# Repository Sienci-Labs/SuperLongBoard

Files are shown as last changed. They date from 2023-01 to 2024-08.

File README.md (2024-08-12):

# SuperLongBoard PCB Design

These are all the raw build files that we're making available to the public so you can see and access the work that's been put in to make the SuperLongBoard as it currently exists. If you'd like to make it yourself, modify it, or suggest improvements feel free. Please note and respect the license we've chosen to distribute it under.

# License

This code has been created within the context of Open Hardware and is licensed under the "CERN-OHL-S v2". Please read more about this in the LICENSE file. You could redistribute and modify this source and make products using it under the terms of the CERN-OHL-S v2. This means stuff like licensing your changes reciprocally, giving attribution to us, and releasing hardware that this code runs on as CERN-OHL-S v2 too. Note that this LICENSE applies on all coding work done in prior commits to-date, and is now being released in good faith that no action will be taken to pursue past work in order to duplicate the work we've put in without having to abide by the License that's now being applied at its first public release.

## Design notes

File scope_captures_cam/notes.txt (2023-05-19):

While running 100mm diamond pattern (all motors move at once.)
SDS00001 - Yellow Cap near X driver, Purple Cap near Y2 Driver
SDS00002 to SDS00007 - Yellow R68, Purple R67
SDS00008 to SDS00010 - Same nets as above, other side of L13
SDS00011 - Add blue on R68, Green on R67. Nothing running.
SDS00012 to SDS00014 - Same as 11, but running steppers only.
SDS00015 to SDS00023 - Same as above, spindle running.

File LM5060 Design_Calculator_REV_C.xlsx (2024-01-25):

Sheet: Instructions
 | © 2014
LM5060 Design Tool- Rev. C
Typical design procedure
Typical applications require multiple passes through the design tool using MOSFET factors such as transient
thermal response and safe operating area curves. Refer to the following application reports for more detail.
LM5060 Datasheet (See "Detailed Design Procedure") (http://www.ti.com/lit/gpn/lm5060)
The basic design process follows:
1. Enter operating conditions.
2. Select MOSFET and current limit parameters.
3. Enter desired UVLO and OVLO values to get recommended resistor values.
4. Review Circuit Characteristics
Notes
1. This worksheet is designed for use with Microsoft Excel 5.0 or later. Its use is intended to assist power supply designers in their
routine, day-to-day calculations.
2. All worksheets have light green inputs cells, white calculated cells, yellow warning cells and red high-risk cells.
3. Formulas and device constants used in the spreadsheet are locked to prohibit them from accidentally being overwritten or deleted.
TEXAS INSTRUMENTS TEXT FILE LICENSE Copyright (c) 2014 Texas Instruments Incorporated All rights reserved not granted herein. Limited License. Texas Instruments Incorporated grants a world-wide, royalty-free, non-exclusive license under copyrights and patents it now or hereafter owns or controls to make, have made, use, import, offer to sell and sell ("Utilize") this software subject to the terms herein. With respect to the foregoing patent license, such license is granted solely to the extent that any such patent is necessary to Utilize the software alone. The patent license shall not apply to any combinations which include this software, other than combinations with devices manufactured by or for TI (“TI Devices”). No hardware patent is licensed hereunder. Redistributions must preserve existing copyright notices and reproduce this license (including the above copyright notice and the disclaimer and (if applicable) source code license limitations below) in the documentation and/or other materials provided with the distribution Redistribution and use in binary form, without modification, are permitted provided that the following conditions are met: * No reverse engineering, decompilation, or disassembly of this software is permitted with respect to any software provided in binary form. * any redistribution and use are licensed by TI for use only with TI Devices. * Nothing shall obligate TI to provide you with source code for the software licensed and provided to you in obje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

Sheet: Design Calculator
LM5060 Hot Swap Design Tool
 | www.ti.com/hotswap
 |  |  | Enter Values in Green Shaded Cells
 |  |  | Calculated Values are shown in White Cells
 |  |  | Yellow and Red cells highlight potential issues with the design. Red highlights items that are higher risk.
 | Step 0: Calculator Tutorials |  | Note: Before proceeding, please watch the video tutorials listed to ensure accurate results from this tool!
 |  |  | Steps 1 & 2: Operating Conditions, Current Limit, & Circuit Breaker (7:41) (https://training.ti.com/node/1133677)
 |  |  | Step 3: MOSFET Selection (9:58) (https://training.ti.com/node/1133673)
 |  |  | Step 4: Startup (10:32) (https://training.ti.com/node/1133664)
 |  |  | Step 5: UVLO, OVLO & PGD Thresholds (4:20) (https://training.ti.com/node/1133681)
 |  |  | LM5060 Datasheet (http://www.ti.com/product/lm5060)
 |  |  | I understand and agree to watch the video tutorials if help is needed. (Choose Yes to enable the calculator.) |  |  | Yes |  |  |  |  | No
 |  |  | Assure to follow the layout and application guidelines listed on the datasheet. |  |  | Yes
 |  |  | *For additional questions not addressed in the videos, please post on E2E.ti.com |  |  |  |  |  |  |  | Yes
 | Step 1: Operating Conditions |  |  | Minimum Input Operating Voltage: VIN(MIN) | 5.5 | V
 |  |  |  | Nominal Input Operating Voltage: VIN(NOM) | 24 | V
 |  |  |  | Maximum Input Operating Voltage: VIN(MAX) | 28 | V
 |  |  |  | Worst Case Reverse Polarity Voltage | 0 | V
 |  |  |  | Maximum Load Current: IOUT(MAX) | 8 | A
 |  |  |  | Maximum Output Load Capacitance: Cload | 2000 | µF
 | Steps 1 & 2: Operating Conditions, Current Limit, & Circuit Breaker (https://training.ti.com/node/1133677) |  |  | Maximum Ambient Operating Temperature: TMAX | 100 | oC
 | Step 2: MOSFET Selection + Current Limit |  |  | Reverse Polarity | NO |  |  |  |  |  | NO
 |  |  |  | MOSFET Name | IRFH7004TRPBF |  |  |  |  |  | YES
 |  |  |  | Back to Back FETs? | NO
 |  |  |  | # of Parallel FETs | 1
 |  |  |  | Minimum Output Pin Resistance | 0 | kΩ
 |  |  |  | Output Pin Resistance: Rout | 10 | kΩ
 |  |  |  | T = 25C Rds-on typical | 1.1 | mΩ
 | Steps 1 & 2: Operating Conditions, Current Limit, & Circuit Breaker (https://training.ti.com/node/1133677) |  |  | T = 25C Rds-on max | 1.1 | mΩ
 |  |  |  | Calculated estimate of T = 25C Rds-on min | 1.1 | mΩ
 |  |  |  | Normalized Rds-on coefficient at Tmin | 1.1
 |  |  |  | Normalized Rds-on coefficient at Tmax | 1.1
 |  |  |  | Rs min (calculated) | 1.23 | kΩ
 |  |  |  | Actual Rs used | 3 | kΩ
 |  |  |  | Minimum Worst-Case Overcurrent Threshold | 27.93 | A
 |  |  |  | Typical Overcurrent Threshold | 43.64 | A
 | Step 3: MOSFET Selection (https://training.ti.com/node/1133673) |  |  | Maximum Worst-Case Overcurrent Threshold | 50.41 | A
 | Step 3: Fault Detection Delay Time |  |  | Gate Charge at Mosfet Vgs= 6.5 Volts | 10.00 | nC |  |  |  |  | NO
 |  |  |  | Safety Margin | 1.5 |  |  |  |  |  | YES
 |  |  |  | Gate Charge at Mosfet Vgs= 6.5 Volts With Margin | 15 | nC
 |  |  |  | Inrush Current Control | YES
 |  |  |  | Desired Maximum Inrush Current | 10000 | mA
 |  |  |  | Recommended Capacitance CGate | 6.2 | nF
 |  |  |  | Actual Capacitor CGate | 4.7 | nF
 |  |  |  | Actual Maximum Inrush Current | 13191.48936 | mA
 | Step 4: Startup (https://training.ti.com/node/1133664) |  |  | Calculated Maximum Slew Rate | 6.595744681 | V/ms
 |  |  |  | Maximum Startup Time | 6.11 | ms
 |  |  |  | Typical Startup Time | 6.30 | ms
 |  |  |  | Minimum Startup Time | 2.97 | ms
 |  |  |  | Minimum Timer Capacitance Ctimer | 21.40 | nF
 |  |  |  | Actual Used Timer Capacitance | 47 | nF
 |  |  |  | Startup Fault Delay Time(Min) | 13.43 | ms
 |  |  |  | Startup Fault Delay Time(Typical) | 15.67 | ms
 |  |  |  | Startup Fault Delay Time(Max) | 23.50 | ms
 |  |  |  | Over-Current Fault Delay Time(Min) | 7.23 | ms
 |  |  |  | Over-Current Fault Delay Time(Typical) | 8.55 | ms
 |  |  |  | Over-Current Fault Delay Time(Max) | 11.06 | ms
 | Step 5: UVLO & OVLO Thresholds |  |  |  | Option A |  |  |  | OPTION A |  | Option A
 |  |  |  |  | Include Hystersis |  |  |  |  |  | Option B
 |  |  |  | Desired Typical OVLO | 28 | V |  |  |  |  | Include Hystersis
 |  |  |  | Desired Typical UVLO | 9 | V |  |  |  |  | No Hysteresis
 |  |  |  | R1 | 20 | kW
 |  |  |  | Recommended Resistance for: R2 | 2.25 | kW
 |  |  |  | Enter the Resistance for R2 | 2.7 | kW
 | Step 5: UVLO, OVLO & PGD Thresholds (https://training.ti.com/node/1133681) |  |  |  | 15.00 | kW
 |  |  |  | Recommended Resistance for R3 | 1.49 | kW
 |  |  |  | Enter the Resistance for R3 | 1.8 | kW
 |  |  |  |  |  |  |  |  | OPTION B
 |  | Resulting Thresholds: | Minimum | Typical | Maximum
 |  | Upper OVLO Threshold = | 25.66 | 27.33 | 29.00 | V
 |  | Lower OVLO Threshold = | 22.40 | 24.07 | 25.73 | V
 |  | Upper UVLO Threshold = | 7.97 | 8.82 | 9.67 | V
 |  | Lower UVLO Threshold = | 6.95 | 8.02 | 9.14 | V
 |  | Note: If any of the cells above are yellow, then these values are outside of the device's operating range. This will result in the device turning either on or off at its operating limits rather than at the user selected values in yellow.
 | Design Summary |  |  | R1 = | 20 | kW
 |  |  |  | R2 = | 2.70 | kW |  |  | Settings | Units
 |  |  |  | R3 = | 1.8 | kW |  | Typical Over-Current Threshold | 43.64 | A
 |  |  |  | Rs = | 3.00 | kW |  | Startup Delay Time | 15.67 | ms
 |  |  |  | R5= | 0 | kW |  | Over-Current Fault Delay | 8.55 | ms
 |  |  |  | R8 = | 1.8 | kW |  | Upper OVLO Threshold | 27.33 | V
 |  |  |  | R9 = | 2.7 | kW |  | Lower OVLO Threshold | 24.07 | V
 |  |  |  | R10 = | 2.7 | kW |  | Upper UVLO Threshold | 8.82 | V
 |  |  |  | R11 = | 1.8 | kW |  | Lower UVLO Threshold | 8.02 | V
 |  |  |  | CTimer = | 47.00 | nF | OPTION B
 |  |  |  | Cin = | 100 | nF
 |  |  |  | CGate = | 4.7 | nF
 |  |  |  | CLoad = | 2000 | µF
 |  |  |  | D1 | SMBJ51A-13-F
 |  |  |  | Q1 | IRFH7004TRPBF
 | Notes: | 1. Although not mandatory, Cin provides transient suppression at the VIN pin
 |  | 2. A TVS clamp from VIN to GND is absolutely mandatory to clamp the voltage overshoot upon MOSFET turn-off, e.g. during circuit breaker
 |  | 3. Componet tolerances not accounted for in Min/Max Calculations.

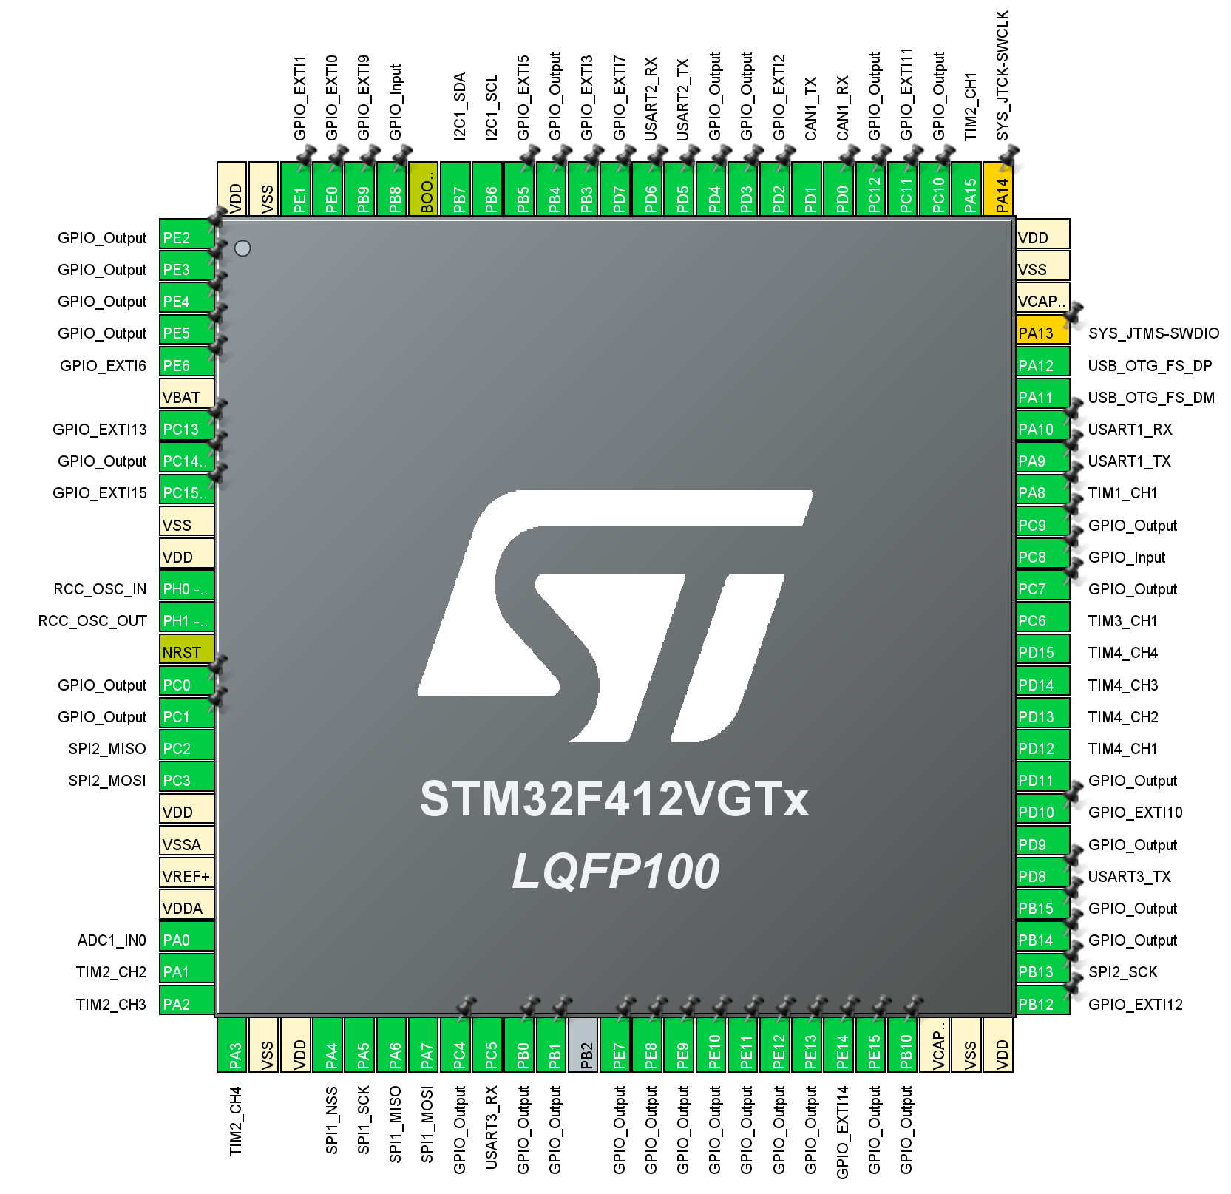
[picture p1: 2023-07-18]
Schematic/stm32f412_img.png

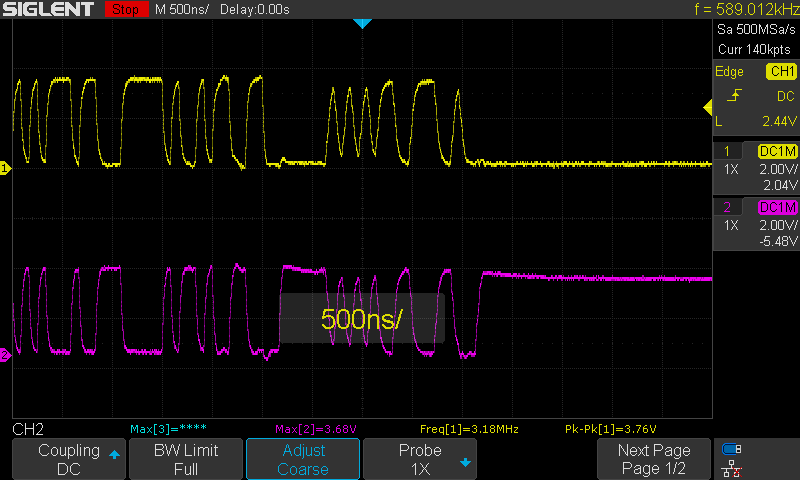
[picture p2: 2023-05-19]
scope_captures_cam/SDS00006.png

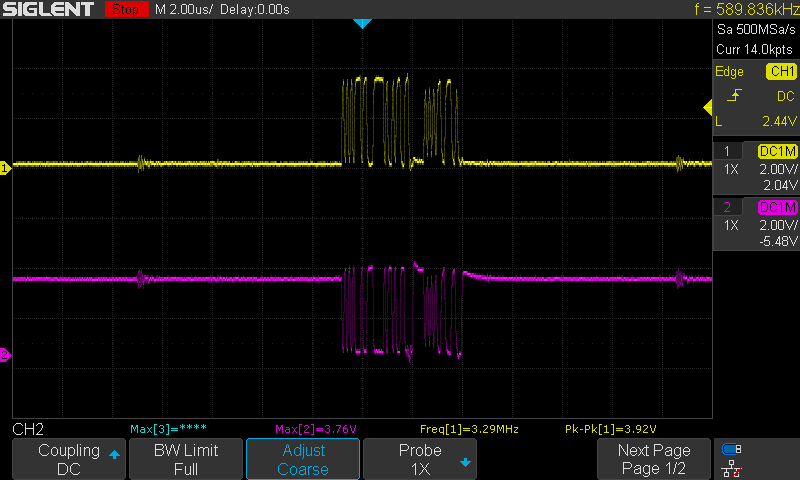
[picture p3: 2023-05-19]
scope_captures_cam/SDS00008.png

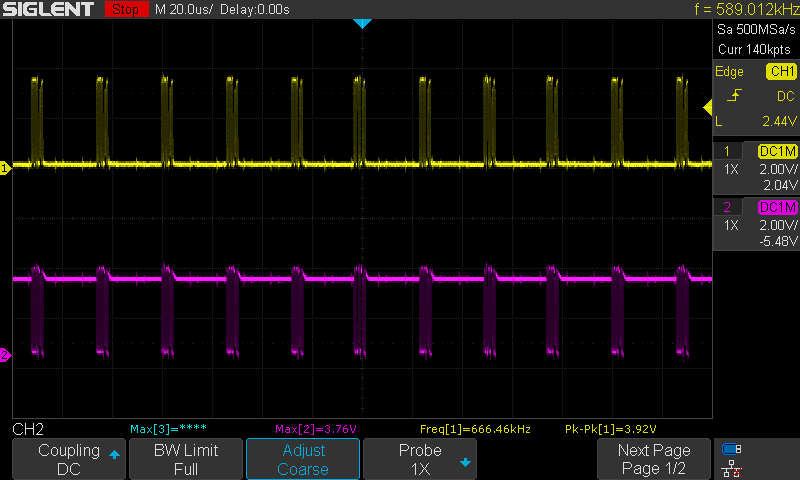
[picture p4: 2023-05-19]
scope_captures_cam/SDS00005.png

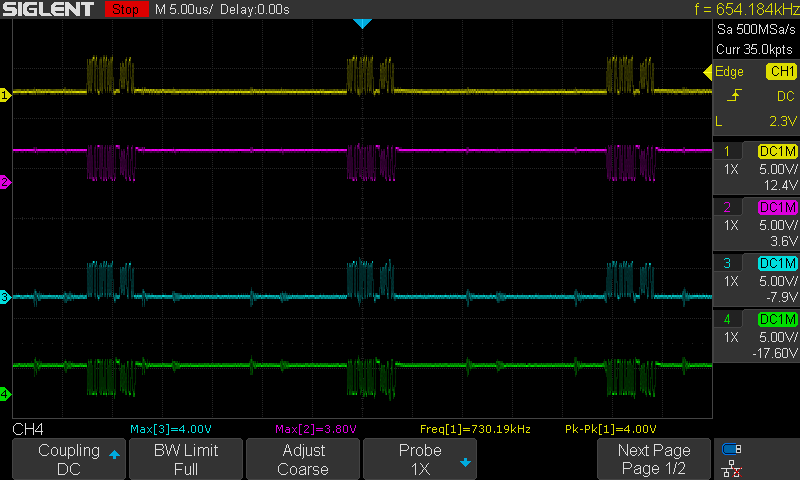
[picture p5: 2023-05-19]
scope_captures_cam/SDS00023.png

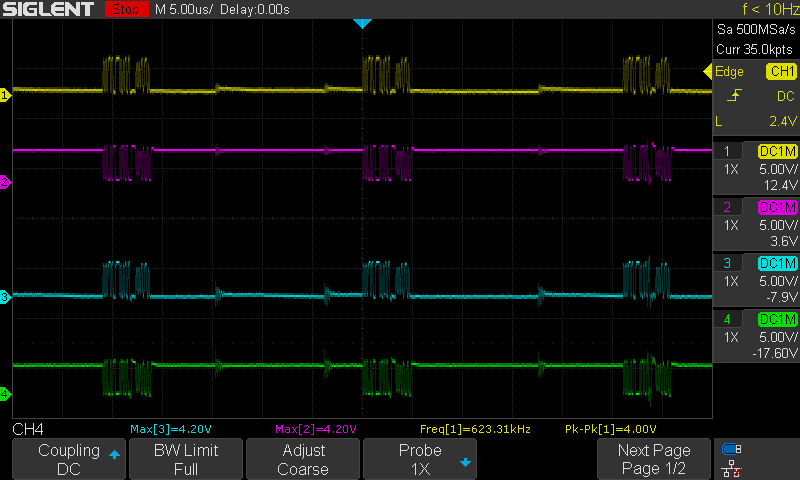
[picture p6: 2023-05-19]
scope_captures_cam/SDS00011.png

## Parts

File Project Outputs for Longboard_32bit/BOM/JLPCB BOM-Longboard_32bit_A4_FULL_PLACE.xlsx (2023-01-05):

Quantity | Manufacturer Part Number | Manufacturer | Description | SuppliersPartNumber | Designator | Comment
70 | CC0603KRX7R9BB104 | YAGEO | Chip capacitors | C14663 | C1, C2, C3_AL, C3_PH_CY, C3_PH_HLT, C3_PH_MA1, C3_PH_MA2, C3_PRB, C3_TLO, C3_XL, C3_Y1L, C3_Y2L, C3_ZL, C4, C10, C20, C21, C22, C24, C29, C30, C31, C32, C33, C34, C35, C36, C37, C42_STEP_A, C42_STEP_X, C42_STEP_Y, C42_STEP_Z, C45_STEP_A, C45_STEP_X, C45_STEP_Y, C45_STEP_Z, C46_STEP_A, C46_STEP_X, C46_STEP_Y, C46_STEP_Z, C47_STEP_A, C47_STEP_X, C47_STEP_Y, C47_STEP_Z, C50_STEP_A, C50_STEP_X, C50_STEP_Y, C50_STEP_Z, C51_STEP_A, C51_STEP_X, C51_STEP_Y, C51_STEP_Z, C65, C66, C68, C69, C70, C71, C72, C73, C80, C81, C82, C86, C90, C93, C94, C95, C96, C99 | 100nF
17 | CL10A105KB8NNNC | Samsung Electro-Mechanics | Chip capacitors | C15849 | C5, C9, C27, C28, C41_STEP_A, C41_STEP_X, C41_STEP_Y, C41_STEP_Z, C62, C63, C64, C67, C74, C85, C89, C92, C98 | 1uF
8 | CL31A106KBHNNNE | Samsung Electro-Mechanics | Chip capacitors | C13585 | C6, C11, C12, C14, C15, C58, C59, C78 | 10uF
2 | CL21A475KAQNNNE | Samsung Electro-Mechanics | Chip capacitors | C1779 | C7, C60 | 4.7uF
9 | CL21A226MAQNNNE | Samsung Electro-Mechanics | Chip capacitors | C45783 | C8, C13, C52, C53, C55, C61, C79, C83, C87 | 22uF
2 | 0603B103K500NT | Guangdong Fenghua Advanced Tech | Chip capacitors | C57112 | C16, C97 | 10nF
5 | CL10C100JB8NNNC | Samsung Electro-Mechanics | Chip capacitors | C1634 | C17, C38, C39, C75, C76 | 10pF
2 | CC0603KRX7R9BB822 | YAGEO | 50V 8.2nF X7R ±10% 0603 Multilayer Ceramic Capacitors MLCC - SMD/SMT ROHS | C113812 | C18, C19 | 8.2nF
7 | CL10A475KO8NNNC | Samsung Electro-Mechanics | Chip capacitors | C19666 | C23, C25, C26, C54, C84, C88, C91 | 4.7uF
4 | CL10B224KA8NNNC | Samsung Electro-Mechanics | Chip capacitors | C21120 | C40_STEP_A, C40_STEP_X, C40_STEP_Y, C40_STEP_Z | 220nF
8 | UUD1H221MNL1GS | Nichicon | CAP ALUM 220UF 20% 50V SMD | C125976 | C43_STEP_A, C43_STEP_X, C43_STEP_Y, C43_STEP_Z, C44_STEP_A, C44_STEP_X, C44_STEP_Y, C44_STEP_Z | 220uF
4 | CL21A106KAYNNNE | Samsung Electro-Mechanics | Chip capacitors | C15850 | C48_STEP_A, C48_STEP_X, C48_STEP_Y, C48_STEP_Z | 10uF
4 | CL10B474KA8NNNC | Samsung Electro-Mechanics | Chip capacitors | C1623 | C49_STEP_A, C49_STEP_X, C49_STEP_Y, C49_STEP_Z | 470nF
1 | TAJB107K006RNJ | AVX | Tantalum capacitor | C16133 | C56 | 100uF
2 | HV101M035E077ETR | Capxon International Elec | -45℃~+105℃ 2000hrs@105℃ 100uF 7.7mm 35V 6.3mm ±20% SMD,6.3x7.7mm Aluminum Electrolytic Capacitors - SMD ROHS | C59934 | C57, C77 | 100uF
1 | DF40HC(3.0)-100DS-0.4V(51) | Hirose | Raspberry Pi Compute Module 4 Pins 1-100 (Connector A) | C424649 | CM1 | Raspberry Pi Compute Module 4-A
1 | DF40HC(3.0)-100DS-0.4V(51) | Hirose | Raspberry Pi Compute Module 4 Pins 101-200 (Connector B) | C424649 | CM2 | Raspberry Pi Compute Module 4-B
7 | 19-217/GHC-YR1S2/3T | Everlight Elec | LED | C72043 | D1, D12, D18, D20, D24, D26, D29 | 0603 Green
4 | 19-213SURC/S530-A3/TR8 | Everlight Elec | 20mA 632nm Colorless transparence 624nm~624nm -40℃~+85℃ Red 120° 60mW 0603 Light Emitting Diodes (LED) ROHS | C72039 | D2, D13, D17, D25 | 0603 Red
9 | 19-213/Y2C-CQ2R2L/3T(CY) | Everlight Elec | LED | C72038 | D3, D4, D5, D6, D7, D8, D9, D10, D11 | 0603 Yellow
2 | SM712 | DOWO | Bidirectional 12V (Max), 7V (Max) 7.5V / 13.3V 10V / 20V 12A(8/20us) SOT-23-3 TVS RoHS | C293966 | D14, D16 | SM712
1 | 19-217UWD/S365-2/TR8 | Everlight Elec | LED | C133759 | D15 | 0603 White
1 | SS54 | MDD | 40V 5A 550mV@5A | C22452 | D19 | SS54
1 | SMAZ27-13-F | Diodes Incorporated | 27V ±5% 1W 500nA @ 20.5V SMA(DO-214AC) Zener Diodes RoHS | C155318 | D21 | SMAZ27-13-F
1 | SSB43L-E3/52T | Vishay Semiconductors | Rectifier Diode Schottky 30V 4A 2-Pin SMB T/R / DIODE SCHOTTKY 30V 4A DO214AA | C222519 | D22 | SSB43L-E3_52T
1 | 1SMAF4734A | Shandong Jingdao Microelectronics | 27V ±5% 1W 500nA @ 20.5V SMA(DO-214AC) Zener Diodes RoHS | C169539 | D23 | 1SMAF4734A
1 | USBLC6-2SC6 | TECH PUBLIC | Very low capacitance ESD protection, 3.5 pF, -40 to 125 degC, 6-Pin SOT23, RoHS, Tape and Reel | C2827654 | D27 | USBLC6-2SC6
1 | SS36-E3/57T | Vishay Intertech | DIODE SCHOTTKY 60V 3A DO214AB | C35722 | D28 | SS36-E3/57T
4 | B5819W SL | Jiangsu Changjing Electronics Technology | Schottky Diode | C8598 | D30_AX_RL1, D30_AX_RL2, D31_AX_TR1, D31_AX_TR2 | B5819W SL
1 | JK-nSMD050-24 | Jinrui Electronic Materials Co. | 24V 1A 0.1s 1206 PTC Resettable Fuses RoHS | C369160 | FUSE1 | 24V 1A
4 | TMC2660C-PA-T | TRINAMIC | QFP-44 Motor Driver ICs ROHS | C2927052 | IC1_STEP_A, IC1_STEP_X, IC1_STEP_Y, IC1_STEP_Z | TMC2660C-PA-T
1 | 95278-101A16LF | Amphenol ICC / FCI | Conn Unshrouded Header HDR 16 POS 2.54mm Solder ST Top Entry SMD BergStik® T/R | C188235 | J1 | 95278-101A16LF
1 | DB2ERC-2.54-3P-GN | DIBO | 150V 5A 3 Bend -40℃~+105℃ Copper Alloy 1 2.54mm Green Board Edge/Receptacle-Close Tin Push-Pull,P=2.54mm Pluggable System Terminal Block ROHS | C2927504 | J2 | DB2ERC-2.54-3P-GN
2 | DB2ERC-2.54-2P-GN | DIBO | 150V 5A 2 Bend -40℃~+105℃ Copper Alloy 1 2.54mm Green Board Edge/Receptacle-Close Tin Push-Pull,P=2.54mm Pluggable System Terminal Block ROHS | C2927503 | J3, J13 | DB2ERC-2.54-2P-GN
5 | B4B-XH-A(LF)(SN) | JST | XH Series 4 Position 2.5 mm Pitch Through Hole Crimp Top Entry Shrouded Header | C144395 | J4, J5, J6, J7, J8 | B4B-XH-A(LF)(SN)
1 | WJ15EDGRC-3.81-5P | Ningbo Kangnex | 3.81mm Green Board Edge/Receptacle-Close Push-Pull,P=3.81mm Pluggable System Terminal Block ROHS | C8395 | J9 | WJ15EDGRC-3.81-5P
2 | WJ15EDGRC-3.81-4P | Ningbo Kangnex Elec | 3.81mm Green Board Edge/Receptacle-Close Push-Pull,P=3.81mm Pluggable System Terminal Block ROHS | C7245 | J10, J34 | WJ15EDGRC-3.81-4P
1 | WJ15EDGRC-3.81-3P | Ningbo Kangnex | 3.81mm Green Board Edge/Receptacle-Close Push-Pull,P=3.81mm Pluggable System Terminal Block ROHS | C8406 | J11 | WJ15EDGRC-3.81-3P
2 | DS1133-S60BPX | CONNFLY Elec | RJ12 RJReceptacle 1 Plugin Ethernet Connectors/Modular Connectors (RJ45 RJ11) ROHS | C77859 | J12, J14 | DS1133-S60BPX
2 | 907-111A1022D10200 | Jing Extension of the Electronic Co. | USB 2.0 2 8 Female Type-A Plugin USB Connectors ROHS | C12049 | J15, J16 | 907-111A1022D10200
1 | 10118194-0001LF | Amphenol ICC (FCI) | CONN RCPT USB2.0 MICRO B SMD R/A | C132563 | J17 | 10118194-0001LF
1 | ARJM11D7-502-AB-EW2 | Abracon LLC | 1 Port RJ45Through Hole 10/100/1000 Base-T, AutoMDIX | 535-14152-ND | J18 | ARJM11D7-502-AB-EW2
1 | 1747981-1 | TE Connectivity | HDMI Receptacle, Pitch 0.5 mm, 19 Position, Height 6.38 mm, RoHS, Tape and Reel | C428484 | J19 | 1747981-1
1 | TYPE-C-31-M-12 | HRO Electronics Co., Ltd. | USB Connectors 24 Receptacle 1 8.94*7.3mm RoHS | C2765186 | J20 | TYPE-C-31-M-12
1 | B3B-XH-A(LF)(SN) | JST Sales America | Connector Header Through Hole 3 position 0.098" (2.50mm) | C144394 | J21 | B3B-XH-A(LF)(SN)
4 | WJ2EDGK-5.08-4P | Ningbo | 4 1 5.08mm Green Plug P=5.08mm Pluggable System Terminal Block ROHS | C71372 | J22, J23, J24, J25 | WJ2EDGK-5.08-4P
6 | WJ15EDGK-3.81-2P | Ningbo | 2 1 3.81mm Green Plug P=3.81mm Pluggable System Terminal Block ROHS | C8466 | J26, J31_AX_RL1, J31_AX_RL2, J32, J33_AX_TR1, J33_AX_TR2 | WJ15EDGK-3.81-2P
1 | WJ15EDGK-3.81-5P | Ningbo Kangnex Elec | 3.81mm Green Plug P=3.81mm Pluggable System Terminal Block ROHS | C3804 | J27 | WJ15EDGK-3.81-5P
1 | WJ15EDGK-3.81-4P | Ningbo | 3.81mm Green Plug P=3.81mm Pluggable System Terminal Block ROHS | C7244 | J28 | WJ15EDGK-3.81-4P
2 | WJ2EDGK-5.08-2P | Kangnex | 5.08mm Green Plug P=5.08mm Pluggable System Terminal Block ROHS | C71370 | J29, J30 | WJ2EDGK-5.08-2P
2 | DB2EK-2.54-2P-GN-S | DIBO | 150V 5A 2 -40℃~+105℃ Copper Alloy 1 2.54mm Green Plug Tin P=2.54mm Pluggable System Terminal Block ROHS | C2927483 | J35, J36 | DB2EK-2.54-2P-GN-S
6 | CBG100505U221T | FH (Guangdong Fenghua Advanced Tech) | Ferrite Bead | C92617 | L1, L2, L4, L5, L10, L11 | 220R @ 100Mhz 100mA
1 | YSPI0630A-220M | YJYCOIN | 3A 22uH ±20% 130mΩ SMD,7.1x6.6x3mm Power Inductors ROHS | C497873 | L3 | 22 uH
3 | CBW201209U221T | FH (Guangdong Fenghua Advanced Tech) | 220Ω @ 100MHz 1 2A 150mΩ 0805 Ferrite Beads ROHS | C139188 | L6, L8, L9 | 220Ω @ 100MHz 1 2A
1 | DLW21HN900SQ2L | Murata Electronics | 90Ω@100MHz -40℃~+85℃ 350mΩ 50V 2 330mA 125V SMD-4P Common Mode Filters ROHS | C80529 | L13 | DLW21HN900SQ2L
1 | 22284020 | MOLEX | Straight Square Pins 2 2.54mm Black Brass 1x2P Plugin,P=2.54mm Pin Headers ROHS | C234182 | P1 | Header
4 | DB2ERC-5.08-4P-GN | Ningbo Kangnex Elec | 5.08mm Green Board Edge/Receptacle-Close Push-Pull,P=5.08mm Pluggable System Terminal Block ROHS | C395753 | P2, P3, P4, P5 | DB2ERC-5.08-4P-GN
6 | WJ15EDGRC-3.81-2P | Ningbo Kangnex | 3.81mm Green Board Edge/Receptacle-Close Push-Pull,P=3.81mm Pluggable System Terminal Block ROHS | C8387 | P6, P18_AX_RL1, P18_AX_RL2, P19, P21_AX_TR1, P21_AX_TR2 | WJ15EDGRC-3.81-2P
1 | DB2EK-2.54-3P-GN-S | DIBO | 150V 5A 3 -40℃~+105℃ Copper Alloy 1 2.54mm Green Plug Tin P=2.54mm Pluggable System Terminal Block ROHS | C2927484 | P7 | DB2EK-2.54-3P-GN-S
4 | PZ254V-12-8P | XFCN | Straight Square Pins 2.5mm 6mm -40℃~+105℃ 3mm 8 2.54mm 双排 Black Brass 2x4P 2.54mm Plugin,P=2.54mm Pin Headers ROHS | C492421 | P10, P12, P13, P14 | Header 4X2
1 | 321040SG0ABK00A01 | JILN | 2.54mm Straight Gold Brass 20 Push - Pull 2.54mm 2 Straight,P=2.54mm IDC Connectors ROHS | C601944 | P11 | 321040SG0ABK00A01
2 | WJ2EDGV-5.08-2P | Kangnex | 5.08mm Green Board Edge/Receptacle-Open Straight,P=5.08mm Pluggable System Terminal Block ROHS | C8461 | P16, P17 | WJ2EDGV-5.08-2P
1 | 61200821621 | Wurth Elektronik | Male Box Header WR-BHD, THT, Vertical, pitch 2.54 mm, 8 pins | C9135 | P20 | C9135
1 | WJ15EDGK-3.81-3P | Ningbo | 3.81mm Green Plug P=3.81mm Pluggable System Terminal Block ROHS | C8413 | P22 | WJ15EDGK-3.81-3P
2 | ST3422A | STANSON Tech. | 60V 6A 28mΩ@10V,6A 2W 3V@250uA 38pF@15V N Channel 455pF@15V 10nC@10V -55℃~+150℃@(Tj) SOT-23-3L MOSFETs ROHS | C2682907 | Q2_AX_RL1, Q2_AX_RL2 | ST3422A
2 | MMBT5551 | Jiangsu Changjing Electronics Technology | 50nA 160V 300mW 200@10mA,5V 600mA 100MHz 200mV@50mA,5mA NPN +150℃@(Tj) SOT-23-3 Bipolar Transistors - BJT ROHS | C2145 | Q3_AX_TR1, Q3_AX_TR2 | MMBT5551
7 | 0603WAF0000T5E | Uniroyal Elec | Chip resistor | C21189 | R2, R3, R4, R9, R130_AX_TR1, R130_AX_TR2, R131 | 0Ω ±1%
11 | 0603WAF2001T5E | Uniroyal Elec | Chip resistor | C22975 | R5, R6, R53, R54, R85, R90, R91, R92, R93, R94, R95 | 2KΩ ±1%
19 | 0603WAF1002T5E | Uniroyal Elec | Chip resistor | C25804 | R8, R24, R28, R30, R55, R61, R62, R77, R82, R83, R106, R125_AX_TR1, R125_AX_TR2, R128_AX_TR1, R128_AX_TR2, R129_STEP_A, R129_STEP_X, R129_STEP_Y, R129_STEP_Z | 10KΩ ±1%
32 | 0603WAF1001T5E | Uniroyal Elec | Chip resistor | C21190 | R11, R12, R13, R14, R15, R16, R17, R18, R19, R20, R21, R23_AL, R23_PH_CY, R23_PH_HLT, R23_PH_MA1, R23_PH_MA2, R23_PRB, R23_TLO, R23_XL, R23_Y1L, R23_Y2L, R23_ZL, R109_AX_RL1, R109_AX_RL2, R110_AX_RL1, R110_AX_RL2, R123_AIN0, R123_AIN1, R123_AIN2, R123_AIN3, R123_ARXD, R123_SAS | 1KΩ ±1%
20 | 0603WAF4701T5E | Uniroyal Elec | Chip resistor | C23162 | R22_AL, R22_PH_CY, R22_PH_HLT, R22_PH_MA1, R22_PH_MA2, R22_PRB, R22_TLO, R22_XL, R22_Y1L, R22_Y2L, R22_ZL, R26, R29, R64, R65, R66, R107, R108, R119, R126 | 4.7KΩ ±1%
26 | 0603WAF5100T5E | Uniroyal Elec | Chip resistor | C23193 | R25, R31, R32, R35, R37, R39, R41, R43, R112, R114, R116, R118, R120, R122_AO0, R122_AO1, R122_AO2, R122_AO3, R122_ATXD, R122_COO, R122_MIS, R124_AIN0, R124_AIN1, R124_AIN2, R124_AIN3, R124_ARXD, R124_SAS | 510Ω ±1%
1 | 0603WAF1003T5E | Uniroyal Elec | Chip resistor | C25803 | R27 | 100KΩ ±1%
1 | 0402WGF4701TCE | Uniroyal Elec | Chip resistor | C25900 | R33 | 4.7KΩ ±1%
16 | 0603WAF3000T5E | Uniroyal Elec | Chip resistor | C23025 | R34, R36, R38, R40, R42, R111, R113, R115, R117, R121_AO0, R121_AO1, R121_AO2, R121_AO3, R121_ATXD, R121_COO, R121_MIS | 300Ω ±1%
9 | 0402WGF5100TCE | Uniroyal Elec | Chip resistor | C25123 | R44, R45, R47, R50, R51, R52, R84, R88, R89 | 510Ω ±1%
2 | 0603WAF5600T5E | Uniroyal Elec | Chip resistor | C23204 | R46, R48 | 560Ω ±1%
1 | 0603WAF1300T5E | Uniroyal Elec | Chip resistor | C22796 | R49 | 130Ω ±1%
1 | 0603WAF4702T5E | Uniroyal Elec | Chip resistor | C25819 | R56 | 47KΩ ±1%
1 | 0603WAF1801T5E | Uniroyal Elec | Chip resistor | C4177 | R57 | 1.8KΩ ±1%
1 | 0402WGF5101TCE | Uniroyal Elec | Chip resistor | C25905 | R58 | 5.1KΩ ±1%
4 | 0402WGF2201TCE | Uniroyal Elec | Chip resistor | C25879 | R59, R60, R101, R102 | 2.2KΩ ±1%
11 | 0603WAF220JT5E | Uniroyal Elec | Chip resistor | C23345 | R63, R67, R68, R69, R70, R71, R72, R73, R74, R75, R76 | 22Ω ±1%
8 | 0603WAF100JT5E | Uniroyal Elec | Chip resistor | C22859 | R78_STEP_A, R78_STEP_X, R78_STEP_Y, R78_STEP_Z, R80_STEP_A, R80_STEP_X, R80_STEP_Y, R80_STEP_Z | 10Ω ±1%
8 | 1206W4F100LT5E | Uniroyal Elec | Chip resistor | C25334 | R79_STEP_A, R79_STEP_X, R79_STEP_Y, R79_STEP_Z, R81_STEP_A, R81_STEP_X, R81_STEP_Y, R81_STEP_Z | 0.1Ω ±1%
5 | 0402WGF4702TCE | Uniroyal Elec | Chip resistor | C25792 | R86, R96, R97, R98, R99 | 47KΩ ±1%
1 | 0805W8F1200T5E | Uniroyal Elec | Chip resistor | C17437 | R87 | 120Ω ±1%
1 | 0402WGF1202TCE | Uniroyal Elec | Chip resistor | C25752 | R100 | 12KΩ ±1%
1 | 0402WGF1502TCE | Uniroyal Elec | Chip resistor | C25756 | R103 | 15KΩ ±1%
2 | 0402WGF4700TCE | Uniroyal Elec | Chip resistor | C25117 | R104, R105 | 470Ω ±1%
2 | 47219-2001 | Molex | Conn Micro SD Card SKT 8 POS 1.1mm Solder RA SMD 0.5A/Contact Embossed T/R | C164170 | SD1, SD2 | 47219-2001
2 | SKRTLAE010 | ALPS | Side Push Type, 250 V, -40 to 90 degC, 3-Pin SMD, RoHS, Tape and Reel | C110293 | SW1, SW2 | SKRTLAE010
1 | SN74AHC1G86DBVR | Texas Instruments | XOR (Exclusive OR) IC 1 Channel SOT-23-5 | C7471 | U1 | SN74AHC1G86DBVR
41 | EL357N(B)(TA)-G | Everlight Elec, Everlight | OPTOISOLATOR 3.75KV TRANS 4-SOP, Optocoupler SOP-4, EL357N(B)(TA)-G, Everlight Electronics | C6649 | U2_AL, U2_PH_CY, U2_PH_HLT, U2_PH_MA1, U2_PH_MA2, U2_PRB, U2_TLO, U2_XL, U2_Y1L, U2_Y2L, U2_ZL, U4, U5, U6, U7, U8, U9, U10, U11, U12, U14, U15, U21, U22, U29, U30, U31, U32, U33_AO0, U33_AO1, U33_AO2, U33_AO3, U33_ATXD, U33_COO, U33_MIS, U34_AIN0, U34_AIN1, U34_AIN2, U34_AIN3, U34_ARXD, U34_SAS | EL357N(B)(TA)-G
1 | LM358DR2G | ON Semiconductor | Dual Op Amp, 5 - 28 V, 8-PinSOIC | C7950 | U3 | LM358DR2G
1 | SN75176BDR | Texas Instruments | RS-485/RS-422 | C7063 | U13 | SN75176BDR
1 | TPS54331DR | Texas Instruments | Switching Voltage Regulators 3A 28V In Step Down SWIFT DC/DC Cnvrtr | C9865 | U16 | TPS54331DR
1 | STM32F412VGT6 | STMicroelectronics | LQFP-100(14x14) Microcontroller Units (MCUs/MPUs/SOCs) ROHS | C727951 | U17 | STM32F412VGT6
3 | 6N137S(TA) | Everlight Elec | 10Mbit/s 75ns,75ns 1 -40℃~+85℃ 5000V 5kV/us DC SMD-8_6.3mm Optocouplers - Logic Output ROHS | C16496 | U18, U20, U27 | 6N137S(TA)
1 | PCA82C250T/YM,118 | NXP Semicon | CAN | C7439 | U19 | CAN/PCA82C250T/YM
1 | USB2514BI-AEZG | Microchip | Microchip USB2514BI-AEZG; USB Controller; 480Mbit/s; USB 2.0; 3.3 V; 36-Pin QFN | C633339 | U23 | USB2514BI-AEZG
1 | FSUSB42MUX | ON Semiconductor / Fairchild | FSUSB42 Series DPDT 4.3 V 480 Mbps SMT Hi Speed USB 2.0 Switch - MSOP-10 | C11355 | U24 | FSUSB42MUX
1 | AP22653QW6-7 | Diodes | ESDA Series 14.2 V 90 pF Automotive Dual Transil ESD Array - SOT-23 | C5157828 | U25 | AP22653QW6-7
1 | AP2331SA-7 | Diodes | AP2331 Series Single Channel 0.2 A Current-Limited Load Switch - SOT-23 | C500764 | U26 | AP2331SA-7
1 | WS2812B-B/W | Worldsemi | Intelligent Control LED Integrated Light Source, 3.5 to 5.3 V, -25 to 80 degC, 4-Pin SMD, RoHS, Tape and Reel | C2761795 | U28 | WS2812B-B/W
1 | ZD24C128A-SSGMB | Zetta | IC EEPROM 128KBIT I2C 8SOIC | C918271 | U35 | ZD24C128A-SSGMB
1 | 74LVC1G07 | Wuxi I-core Elec | IC BUF NON-INVERT 5.5V SOT353 | C5138996 | U36 | 74LVC1G07
1 | AMS1117-3.3 | AMS | Vout=3.3V 1A 72dB@(120Hz) (LDO) | C6186 | VR1 | AMS1117-3.3
1 | XF-508P-B | XFCN | Fuse Holder, 20 A, 500 V, -50 to 145 degC, 4-Pin THD, RoHS | C2935468 | XF1 | XF-508P-B
1 | TAXM25M4RDBCCT2T | TAE(Zhejiang Abel Elec) | 25MHz SMD Crystal Resonator 10pF 40Ω ±10ppm ±20ppm SMD3225-4P Crystals ROHS | C403946 | Y1 | 25.0 MHz
1 | S3224000201060 | JGHC | 24MHz SMD Crystal Resonator 20pF 60Ω ±10ppm -40℃~+85℃ SMD3225-4P Crystals ROHS | C390771 | Y2 | 24.0 MHz

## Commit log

2022-11-11 Initial commit of WIP design.
    [12V_Power_Supply.SchDoc, 2xparallelswitch.SchDoc, 5V_Isolated_Power_Supply.SchDoc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]
2022-11-11 Commit updates.
    [Block_diagram.SchDoc, CANBUS_Pendant.SchDoc, Compute_Module_EXT_INTERFACES.SchDoc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]
2022-11-12 Update parts for LCSC and 3.81/5.08mm connectors
    [2xparallelswitch.SchDoc, 5V_Power_Supply.SchDoc, Aux_Outputs.SchDoc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]
2022-11-14 Update parts for availability
    [2xparallelswitch.SchDoc, 5V_Power_Supply.SchDoc, Aux_Outputs.SchDoc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]
2022-11-15 Update parts
    [2xparallelswitch.SchDoc, Aux_Outputs.SchDoc, Change Log.SchDoc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]
2022-11-15 Fixing missing footprint
    [Compute_Module_EXT_INTERFACES.SchDoc]
2022-11-17 Commit updates to power supplies and stepper sense resistors.
    [DC_Power_Regulation.SchDoc, Longboard_32bit.PrjPCB, Longboard_32bit.SchDoc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]
2022-11-18 Commit additional power supply updates.
    [2xparallelswitch.SchDoc, 5V_Isolated_Power_Supply.SchDoc, 5V_Isolated_Power_Supply_samples.SchDoc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]
2022-11-20 Commit latest updates.
    [Aux_Outputs.SchDoc, Block_diagram.SchDoc, CANBUS_Pendant.SchDoc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]
2022-11-24 Commit CM4 updated schematics.
    [Compute_Module_EXT_INTERFACES.SchDoc, Compute_Module_POWER.SchDoc, Compute_Module_TOP.SchDoc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]
2022-11-26 Commit updates based on feedback.
    [2xparallelswitch.SchDoc, AUX_40pin.SchDoc, Aux_Outputs.SchDoc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]
2022-11-30 Kept working.
    [5V_Digital_Out.SchDoc, Aux_Outputs.SchDoc, Block_diagram.SchDoc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]
2022-12-01 Commit more updates.
    [5V_Digital_In.SchDoc, Aux_Outputs.SchDoc, CANBUS_Pendant.SchDoc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]
2022-12-01 Commit additional outjobs.
    [Longboard_32bit.PrjPCB]
2022-12-01 Updated page numbers.
    [5V_Digital_In.SchDoc, 5V_Digital_Out.SchDoc, 5V_Power_Supply.SchDoc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]
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2022-12-07 Swapped connectors Replaced CM4 module with two connectors for BOM inclusion
    [3V3_Digital_Out.SchDoc, 5V_Digital_In.SchDoc, 5V_Digital_Out.SchDoc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]
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2022-12-30 Commit WIP layout and slight schematic updates (page numbers)
    [3V3_Digital_Out.SchDoc, 5V_Digital_Out.SchDoc, 5V_Power_Supply.SchDoc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]
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2023-01-03 Commit some updates ahead of adding testpoints.
    [5V_Power_Supply.SchDoc, Compute_Module_CAMERA.SchDoc, Compute_Module_EXT_INTERFACES.SchDoc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]
2023-01-03 Commit schematic updates after review.
    [5V_Power_Supply.SchDoc, Aux_Outputs.SchDoc, Block_diagram.SchDoc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]
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2023-01-04 Replaced D22 with lower forward drop schottkey. I changed pin numbers so it should match previous, but it should be slightly smaller as a bonus. R43 was showing NOT_FITTED in the variants, but I'm 99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
    [Compute_Module_EXT_INTERFACES.SchDoc, DC_Power_Regulation.SchDoc, I2C_Keypad.SchDoc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]
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2023-01-04 Flip L13 along X and remove PCB logos
    [Title Sheet.SchDoc, USB_Connector.SchDoc]
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2023-01-04 Add L6 filter for USB Replaced J18 with ARJM11D7-502-AB-EW2 for magnetics
    [Change Log.SchDoc, Compute_Module_EXT_INTERFACES.SchDoc, Compute_Module_TOP.SchDoc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]
2023-01-04 Changed vertical DB2EVC-2.54-2P-GN to right angle DB2ERC-2.54-2P-GN Changed vertical DB2EVC-2.54-3P-GN to right angle DB2ERC-2.54-3P-GN Add plugs for 2.54mm
    [Aux_Outputs.SchDoc, Change Log.SchDoc, JLPCB BOM-Longboard_32bit_A4_FULL_PLACE.xlsx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]
2023-01-05 Fill out MFG and MFG Part Numbers
    [3V3_Digital_Out.SchDoc, 5V_Digital_Out.SchDoc, 5V_Power_Supply.SchDoc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]
2023-01-05 Change R9 to FITTED Change R10 to NOT_FITTED Changed B3B-XH-A(LF)(SN) to B4B-XH-A(LF)(SN)
    [Change Log.SchDoc, JLPCB BOM-Longboard_32bit_A4_FULL_PLACE.xlsx, Limit_Switches.SchDoc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]
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2023-01-05 Commit repo used to generate A4 CAM files.
    [3V3_Digital_Out.SchDoc, 5V_Digital_Out.SchDoc, 5V_Power_Supply.SchDoc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]
2023-02-13 Commit layer fixes.
    [Aux_Outputs.SchDoc, DC_Power_Regulation.SchDoc, Limit_Switches.SchDoc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]
2023-06-09 Commit fixes for various Jira issues.
    [3V3_Digital_Out.SchDoc, 5V_Digital_Out.SchDoc, 5V_Power_Supply.SchDoc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]
2023-06-14 Commit additional schematic updates.
    [5V_Power_Supply.SchDoc, CANBUS_Pendant.SchDoc, DC_Power_Regulation.SchDoc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]
2023-07-18 Commit latest updates that remove Compute module.
    [Aux_Outputs.SchDoc, Block_diagram.SchDoc, CANBUS_Pendant.SchDoc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]
2023-07-18 Relocated Door signal to limit page.
    [Block_diagram.SchDoc, DC_Power_Regulation.SchDoc, Limit_Switches.SchDoc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]
2023-07-19 Commit a bunch of updates for today.
    [Aux_Outputs.SchDoc, Block_diagram.SchDoc, DC_Power_Regulation.SchDoc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]
2023-07-21 Commit latest B3 updates.
    [Aux_Outputs.SchDoc, Block_diagram.SchDoc, Board_Diagram.SchDoc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]
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2023-07-27 Added net classes for diff pairs.
    [Ethernet_Interface.SchDoc, USB_Connector.SchDoc]
2023-07-28 Update parts for availability and BOM cleanup
    [3V3_Digital_Out.SchDoc, 5V_Digital_Out.SchDoc, 5V_Power_Supply.SchDoc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]
2023-08-01 Schematic tidy up and parts info updates
    [3V3_Digital_Out.SchDoc, 5V_Digital_Out.SchDoc, Block_diagram.SchDoc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]
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2023-08-02 Schematic and component cleanup
    [3V3_Digital_Out.SchDoc, 5V_Digital_Out.SchDoc, 5V_Power_Supply.SchDoc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]
2023-08-02 Reverted J1 back to SMD 95278-101A16LF
    [DC_Power_Regulation.SchDoc, Ethernet_Interface.SchDoc, Longboard_32bit.PrjPCB]
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2023-08-03 Commit updated pinouts and ADC biasing.
    [Aux_Outputs.SchDoc, Limit_Switches.SchDoc, Longboard_32bit.PrjPCB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]
2023-08-03 Update LEDS with correct LED colour.
    [CANBUS_Pendant.SchDoc, DC_Power_Regulation.SchDoc, External_Stepper.SchDoc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]
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2023-08-04 Commit B4 ahead of MFG generation.
    [Block_diagram.SchDoc]
2023-08-04 Commit small and final updates.
    [Longboard_32bit.PrjPCB]
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2023-10-02 Rev B4.1 Replaced Q4-Q7 with 2N7002-7-F
    [Aux_Outputs.SchDoc, Change Log.SchDoc, Longboard_32bit.PrjPCB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]
2023-10-16 Commit current B5 WIP
    [CANBUS_Pendant.SchDoc, Change Log.SchDoc, DC_Power_Regulation.SchDoc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]
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2023-10-30 Commit current B5 WIP.
    [Change Log.SchDoc, Spindle_Control.SchDoc]
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2023-11-03 Commit small FET update.
    [Relay_Driver.SchDoc, Transistor_Driver.SchDoc]
2023-11-07 Updated parts for availability Changed R126 to 12K as per SL-61
    [3V3_Digital_Out.SchDoc, 5V_Digital_Out.SchDoc, 5V_Power_Supply.SchDoc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]
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2023-11-15 Commit B5 package files.
    [5V_Power_Supply.SchDoc, DC_Power_Regulation.SchDoc, Longboard_32bit.PrjPCB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]
2023-11-28 Commit small update for isolator.
    [Aux_Outputs.SchDoc, External_Stepper.SchDoc, Longboard_32bit.PrjPCB]
2024-01-28 Commit latest ahead of generating files.
    [Aux_Outputs.SchDoc]
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2024-01-30 Commit BOM updates for B6.1
    [Longboard_32bit.PrjPCB]
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
